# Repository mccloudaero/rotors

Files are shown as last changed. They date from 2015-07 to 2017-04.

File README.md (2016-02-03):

#Rotor Design and Build Repository
McCloud Aero Corporation

This repository contains the rotor designs and rotor analysis software created by McCloud Aero Corporation. The specific rotor designs contained in this repository were intended for use with the Goliath gas powered quadcopter, but the rotors could be used for other applications.  Goliath uses four rotors with two rotating clockwise (CW) and two counter-clockwise (CCW).  Any use of the data contained in this repository is without warranty.

##Repository Contents
 Documentation (this readme.txt file)
 Rotor Blade Element Analysis (RBEA) software (/rbea)
 Alpha Rotor Design and Build Files (/alpha)
  Counter-Clockwise Version (/CCW)
  Clockwise Version (/CW)
 Beta Rotor Design and Build Files  (/beta)
  Counter-Clockwise Version (/CCW)
  Clockwise Version (/CW)
 Crush Plate Designa and Build Files (/common)

###Alpha Rotor
The Alpha rotor was the original rotor design used for the Goliath quadcopter. This rotor has been tested approximatly 20 times and experienced thrust loads up to 50 lbs. This rotor has not seen long term testing. The pitch was found to be too large and required too much power at the proper RPM for Goliath. It could be applied to other vehicles.

###Beta Rotor
A redesign of the alpha rotor, with the pitch at the tip reduced.  Has not been tested.
 
###Design Files
Each rotor contains the following Design Files:<br>
 *.AD_PRT		- CAD file, Cubify Design Native CAD format (The software used to design the rotors)<br>
 *.stp			- CAD file, STEP format<br>
 *.igs			- CAD file, IGES format<br>
 *_final.stl		- STL file of the final rotor shape<br>
 *_mill_shape.stl	- STL file of the shape to be milled<br>
 *.png			- Image of the rotor design<br>
 
##Design Process
The CAD was built using Cubify Design. The STL file was generated using the folowing settings:<br>
 Units: Inches<br>
 Format: ASCII<br>
 Normal Deviation: 2.0 deg<br>
 Surface Deviation: 0.02<br>
 Maximum Cell Size: 0.5<br>

To create the mill shape in the CAD file:<br>
 1. Unsuppress the Machine Supports
 2. Unsuppress the Hub Support
 3. Unsuppress the Hub Support Mirror
 4. Suppress the Mounting Holes
 5. Suppress the Center Hole
 6. Suppress the Trim Tip

##Toolpath Generation
The toolpaths contained in this repository were generated using MeshCam (http://www.grzsoftware.com/). The rough steps used to create the toolpaths are below.  Feed Rates and plunge rates were driven by the need to go slower though the birch stiffness present in the propeller blanks.

 1. Load mill shape
 2. Choose 2-Sided Maching
 3. Define Stock Size 38" x 10" x 1.75"
 4. Create Top & Bottom Rough Tool Paths with 0.25" diameter tool
  1. Depth per Pass 0.25"
  2. Stepover 0.125"
  3. Feed Rate 60 in/min 
  4. Plunge Rate 10 in/min
  5. Stock to leave 0.05"
 5. Create Top and Bottom Finish X Only Tool Paths with 0.25" diameter tool
  1. Stepover 0.0.0833"
  2. Feed Rate 60 in/min 
  3. Plunge Rate 10 in/min
 6. Create Top and Bottom Finish X Only Tool Paths with 0.25" diameter tool
  1. Stepover 0.0.0833"
  2. Feed Rate 60 in/min 
  3. Plunge Rate 10 in/min

##Build Process
For each rotor there are two STL files, one is the milled shape and the second is the final rotor shape. Each rotor is machined out of a 38" x 10" x 1.75" foam block.  The machining region is 36" x 8" x 1.75", leaving an inch extra on each of the side and no extra on the top and bottom. To machine the part double sided accurately, alignment pins are helpful.  To use the pins, the same alignment holes drilled into rotor need to be drilled into the spoil board (if possible).  Dowel rods (1/4" diameter) are used as alignment pins.

Tool bits needed are:
1/4" End Mill  (>=1.75" Long) for the Finishing Passes

###Machining Steps
 1. Machine the Top
  1. Roughing pass: Start with the 1/2" End Mill and run rotor_XXX_top_rough
  2. Finishing pass (X direction): Switch to 1/4" End Mill and run rotor_XXX_top_finish_x_only
  3. Finishing pass (Y direction): Run rotor_XXX_top_finish_y_only
  4. Drill the Alignment Holes: Run rotor_XXX_top_drill_holes
 2. Flip the block over and re-mount using the alignment holes and pins
 3. Machine the Bottom
  1. Roughing pass: Run rotor_XXX_bottom_rough (Note: roughing stays with 1/4" bit because of the fragile part)
  2. Finishing pass (X direction): Run rotor_XXX_bottom_finish_x_only
  3. Finishing pass (Y direction): Run rotor_XXX_bottom_finish_y_only

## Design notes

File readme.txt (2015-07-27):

Rotor Design and Build Repository
McCloud Aero Corporation

This repository contains the rotor designs and rotor analysis software created by McCloud Aero Corporation. The specific rotor designs contained in this repository were intended for use with the Goliath gas powered quadcopter, but the rotors could be used for other applications.  Goliath uses four rotors with two rotating clockwise (CW) and two counter-clockwise (CCW).  Any use of the data contained in this repository is without warranty.

==Repository Contents==
 Documentation (this readme.txt file)
 Rotor Blade Element Analysis (RBEA) software (/rbea)
 Alpha Rotor Design and Build Files (/alpha)
  Counter-Clockwise Version (/CCW)
  Clockwise Version (/CW)
 Beta Rotor Design and Build Files  (/beta)
  Counter-Clockwise Version (/CCW)
  Clockwise Version (/CW)
 Crush Plate Designa and Build Files (/common)

== Alpha Rotor ==
The Alpha rotor was the original rotor design used for the Goliath quadcopter. This rotor has been tested approximatly 20 times and experienced thrust loads up to 50 lbs. This rotor has not seen long term testing. The pitch was found to be too large and required too much power at the proper RPM for Goliath. It could be applied to other vehicles.

== Beta Rotor ==
A redesign of the alpha rotor, with the pitch at the tip reduced.  Has not been tested.
 
==Design Files==
Each rotor contains the following Design Files:
 *.AD_PRT		- CAD file, Cubify Design Native CAD format (The software used to design the rotors)
 *.stp			- CAD file, STEP format
 *.igs			- CAD file, IGES format
 *_final.stl		- STL file of the final rotor shape
 *_mill_shape.stl	- STL file of the shape to be milled
 *.png			- Image of the rotor design
 
==Design Process==
The CAD was built using Cubify Design. The STL file was generated using the folowing settings:
 Units: Inches
 Format: ASCII
 Normal Deviation: 2.0 deg
 Surface Deviation: 0.02
 Maximum Cell Size: 0.5

To create the mill shape in the CAD file:
1) Unsuppress the Machine Supports 
2) Unsuppress the Hub Support
3) Unsuppress the Hub Support Mirror
4) Suppress the Mounting Holes
5) Suppress the Center Hole
6) Suppress the Trim Tip

==Toolpath Generation==
The toolpaths contained in this repository were generated using MeshCam (http://www.grzsoftware.com/). The rough steps used to create the toolpaths are below.  Feed Rates and plunge rates were driven by the need to go slower though the birch stiffness present in the propeller blanks.

1) Load mill shape
2) Choose 2-Sided Maching
3) Define Stock Size 38" x 10" x 1.75"
4) Create Top & Bottom Rough Tool Paths with 0.25" diameter tool
 A) Depth per Pass 0.25"
 B) Stepover 0.125"
 C) Feed Rate 60 in/min 
 D) Plunge Rate 10 in/min
 E) Stock to leave 0.05"
5) Create Top and Bottom Finish X Only Tool Paths with 0.25" diameter tool
 A) Stepover 0.0.0833"
 B) Feed Rate 60 in/min 
 C) Plunge Rate 10 in/min
6) Create Top and Bottom Finish X Only Tool Paths with 0.25" diameter tool
 A) Stepover 0.0.0833"
 B) Feed Rate 60 in/min 
 C) Plunge Rate 10 in/min

==Build Process==
For each rotor there are two STL files, one is the milled shape and the second is the final rotor shape. Each rotor is machined out of a 38" x 10" x 1.75" foam block.  The machining region is 36" x 8" x 1.75", leaving an inch extra on each of the side and no extra on the top and bottom. To machine the part double sided accurately, alignment pins are helpful.  To use the pins, the same alignment holes drilled into rotor need to be drilled into the spoil board (if possible).  Dowel rods (1/4" diameter) are used as alignment pins.

Tool bits needed are:
1/4" End Mill  (>=1.75" Long) for the Finishing Passes

==Machining Steps==
1) Machine the Top
 A) Roughing pass: Start with the 1/2" End Mill and run rotor_XXX_top_rough
 B) Finishing pass (X direction): Switch to 1/4" End Mill and run rotor_XXX_top_finish_x_only
 C) Finishing pass (Y direction): Run rotor_XXX_top_finish_y_only
 D) Drill the Alignment Holes: Run rotor_XXX_top_drill_holes
2) Flip the block over and re-mount using the alignment holes and pins
3) Machine the Bottom
 A) Roughing pass: Run rotor_XXX_bottom_rough (Note: roughing stays with 1/4" bit because of the fragile part)
 B) Finishing pass (X direction): Run rotor_XXX_bottom_finish_x_only
 C) Finishing pass (Y direction): Run rotor_XXX_bottom_finish_y_only

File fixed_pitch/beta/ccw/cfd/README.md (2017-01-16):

#CFD Analysis

#. Create simplified geometry (CAD)
##. Export as STEP 214
#. Mesh simplified geometry (gmsh)

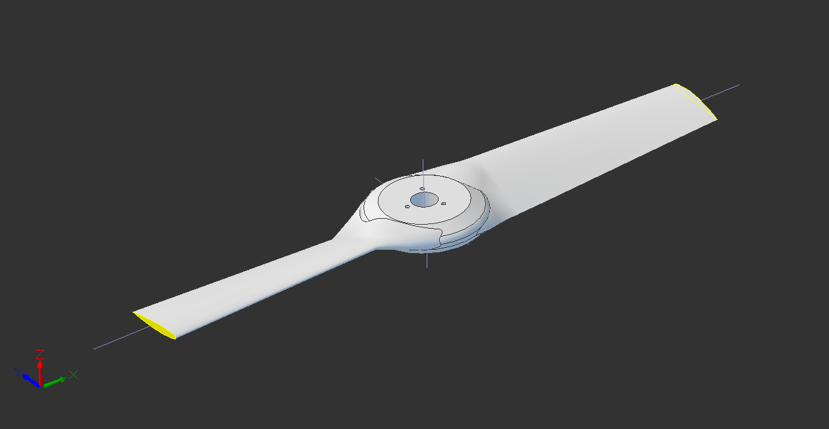
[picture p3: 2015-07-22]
fixed_pitch/beta/CCW/rotor_ccw.png

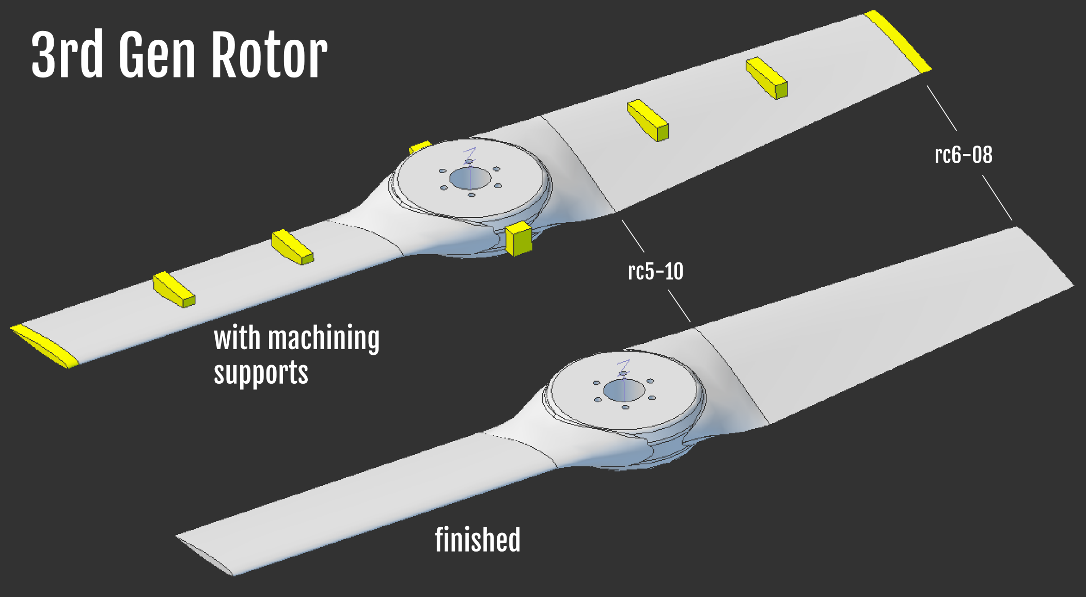
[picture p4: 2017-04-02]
fixed_pitch/gamma/ccw/rotor_before_and_after.png

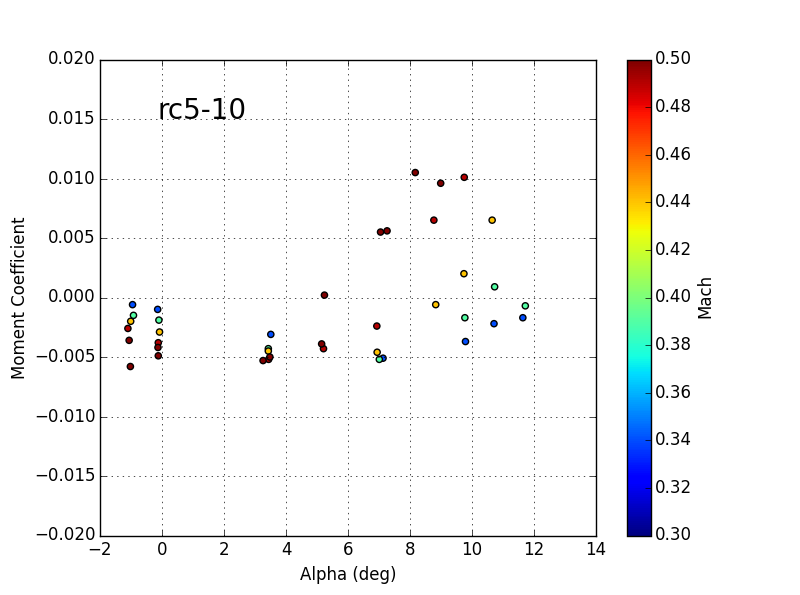
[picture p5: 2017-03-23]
rbea/airfoils/rc5_10_moment.png

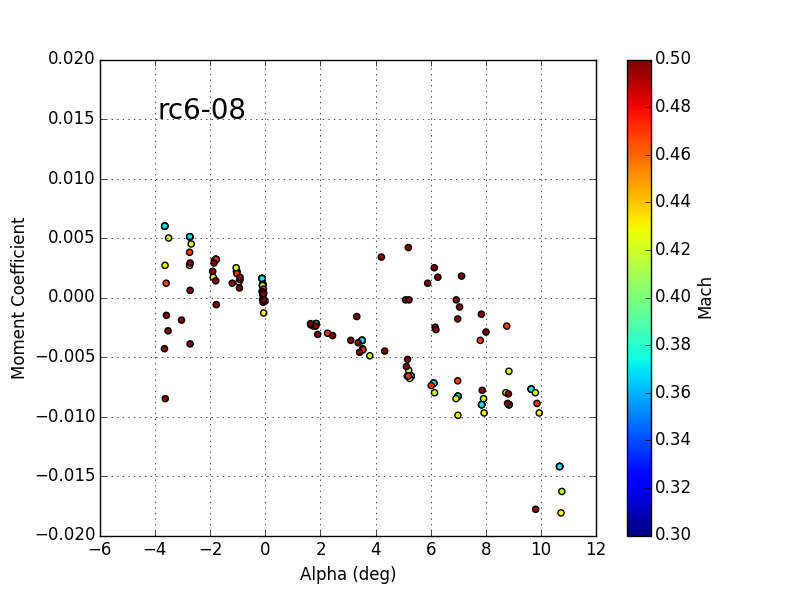
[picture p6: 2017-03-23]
rbea/airfoils/rc6-08_moment.png

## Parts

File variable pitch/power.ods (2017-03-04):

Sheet: Power Budget
Power Budget
Item | mA | Voltage | Count | Watts | Source
Servos | 900 | 6.00 | 2 | 10.8 | https://www.quora.com/Which-battery-should-I-use-to-power-5-servo-MG996R-motors
ESP32 | 260 | 3.30 | 1 | 0.858 | https://cdn.sparkfun.com/datasheets/IoT/esp32_datasheet_en.pdf
 |  |  | Total | 11.658

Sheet: Coil Sizing
Coil Sizing
Min Power | 12 | Watts
Min Voltage | 5 | Volts
Current | 2.4 | Amps
# of Coils | 6
Current per Coil | 0.4 | -> | 25 Gauge min
Turns per Coil | 100
RPM | t | Vmax
3000 | 0.0033333333 | 8.10
3740 | 0.0026737968 | 10.10
3940 | 0.0025380711 | 10.64

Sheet: Magnet Wire Data
Gauge | Resistance (Ohms/1000 ft) | Resistance (Ohms/km) | Max Current Amps)
0000 (4/0) | 0.049 | 0.16072 | 302
000 (3/0) | 0.0618 | 0.202704 | 239
00 (2/0) | 0.0779 | 0.255512 | 190
0 (1/0) | 0.0983 | 0.322424 | 150
1 | 0.1239 | 0.406392 | 119
2 | 0.1563 | 0.512664 | 94
3 | 0.197 | 0.64616 | 75
4 | 0.2485 | 0.81508 | 60
5 | 0.3133 | 1.027624 | 47
6 | 0.3951 | 1.295928 | 37
7 | 0.4982 | 1.634096 | 30
8 | 0.6282 | 2.060496 | 24
9 | 0.7921 | 2.598088 | 19
10 | 0.9989 | 3.276392 | 15
11 | 1.26 | 4.1328 | 12
12 | 1.588 | 5.20864 | 9.3
13 | 2.003 | 6.56984 | 7.4
14 | 2.525 | 8.282 | 5.9
15 | 3.184 | 10.44352 | 4.7
16 | 4.016 | 13.17248 | 3.7
17 | 5.064 | 16.60992 | 2.9
18 | 6.385 | 20.9428 | 2.3
19 | 8.051 | 26.40728 | 1.8
20 | 10.15 | 33.292 | 1.5
21 | 12.8 | 41.984 | 1.2
22 | 16.14 | 52.9392 | 0.92
23 | 20.36 | 66.7808 | 0.729
24 | 25.67 | 84.1976 | 0.577
25 | 32.37 | 106.1736 | 0.457
26 | 40.81 | 133.8568 | 0.361
27 | 51.47 | 168.8216 | 0.288
28 | 64.9 | 212.872 | 0.226
29 | 81.83 | 268.4024 | 0.182
30 | 103.2 | 338.496 | 0.142
31 | 130.1 | 426.728 | 0.113
32 | 164.1 | 538248 | 0.091
33 | 206.9 | 678.632 | 0.072
34 | 260.9 | 855.752 | 0.056
35 | 329 | 1079.12 | 0.044
36 | 414.8 | 1360 | 0.035
37 | 523.1 | 1715 | 0.0289
38 | 659.6 | 2163 | 0.0228
39 | 831.8 | 2728 | 0.0175
40 | 1049 | 3440 | 0.0137

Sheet: Baseline Design
RPM | Voltage | Current | Watts | t | AB
512 | 2 | 1 | 2 | 1.95E-02 | 0.0001302083
818 | 4.78 | 1.47 | 7 | 1.22E-02 | 0.000194784
1022 | 6.8 | 1.7 | 11.7 | 9.78E-03 | 0.0002217873
1288 | 9.5 | 2 | 19 | 7.76E-03 | 0.0002458592
1611 | 12.8 | 2.3 | 29.4 | 6.21E-03 | 0.0002648459
1992 | 16.6 | 2.7 | 45 | 5.02E-03 | 0.0002777778
# of Coils | 6
Current per Coil | 0.35
Turns per Coil | 300

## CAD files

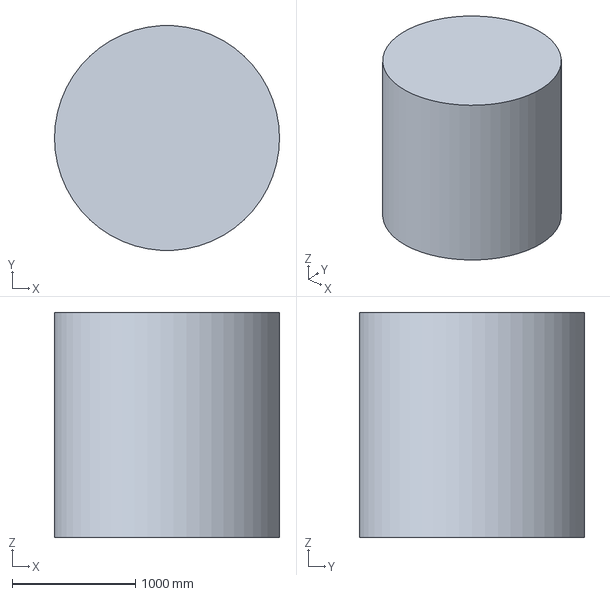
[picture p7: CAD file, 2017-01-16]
fixed_pitch/beta/ccw/cfd/rotor_ccw_cfd_domain.stp
1828.8 x 1825.7 x 1828.8 mm

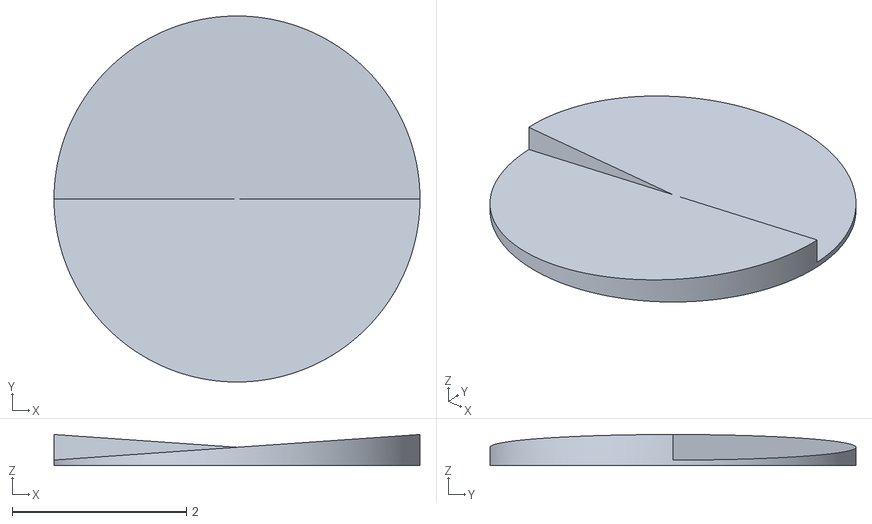
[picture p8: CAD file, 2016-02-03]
adjustment plate/adjustment_plate_cw_no_holes.stl
4.20 x 4.20 x 0.356

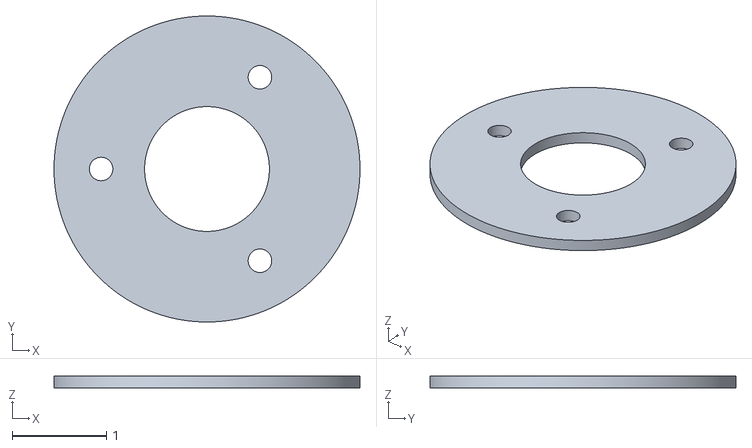
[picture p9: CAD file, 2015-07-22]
common/crush_plate/crush_plate.stl
3.25 x 3.25 x 0.125

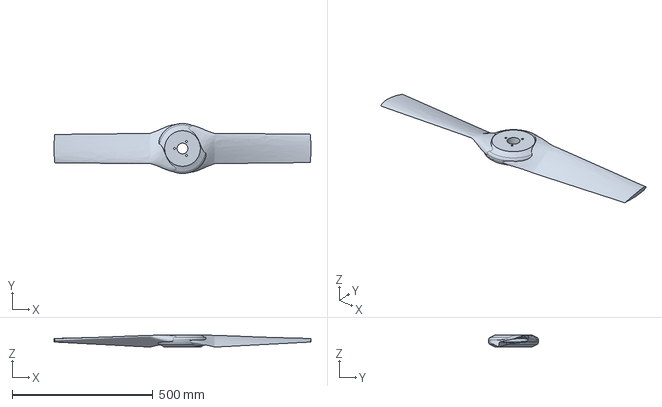
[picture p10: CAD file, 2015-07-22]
fixed_pitch/beta/CCW/rotor_ccw.stp
914.4 x 177.7 x 44.5 mm

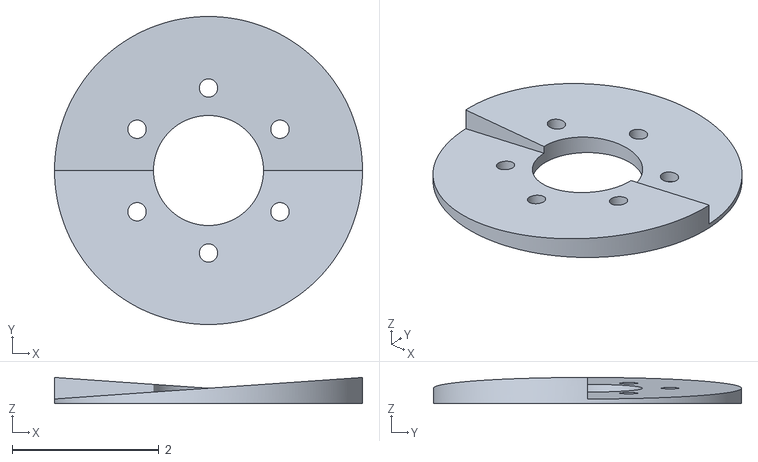
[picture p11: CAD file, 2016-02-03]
adjustment plate/adjustment_plate_cw_with_holes.stl
4.20 x 4.20 x 0.356

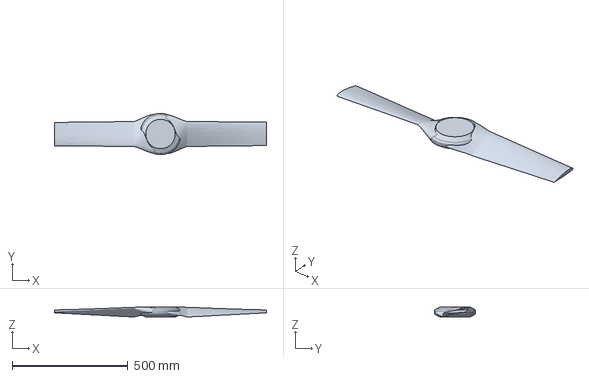
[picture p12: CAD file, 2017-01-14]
fixed_pitch/beta/ccw/cfd/rotor_ccw_cfd_clean.stp
914.4 x 177.7 x 44.5 mm

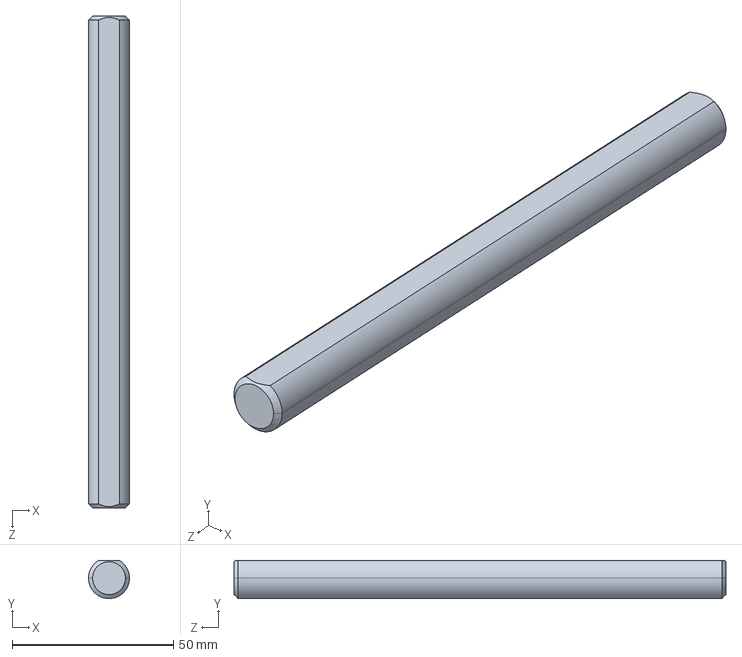
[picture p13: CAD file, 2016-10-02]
variable pitch/design_A/8632T146_D-PROFILE SHAFT.STEP
12.7 x 11.8 x 152.4 mm

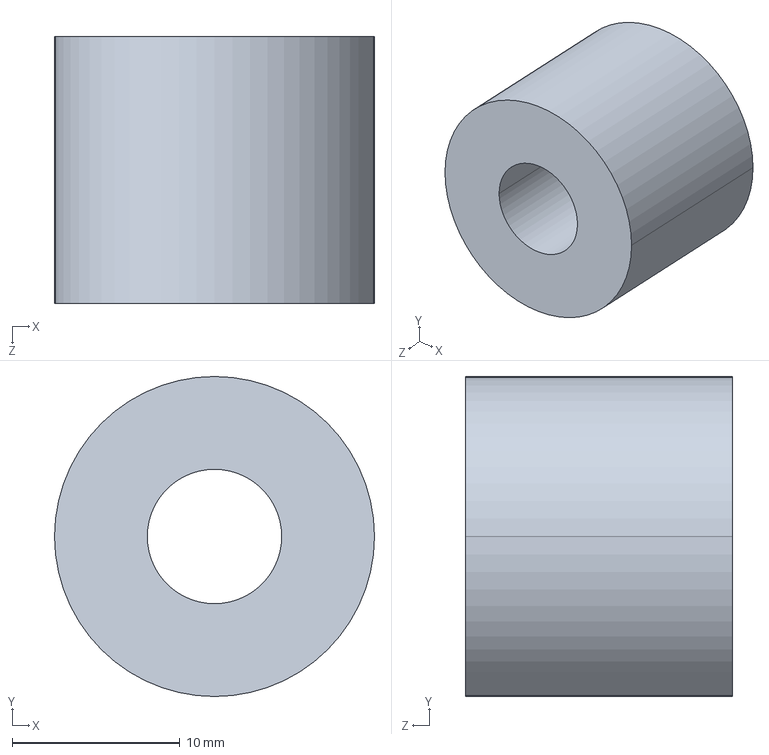
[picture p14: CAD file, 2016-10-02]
variable pitch/design_B/92320A728_SS UNTHRD SPACER.STEP
19.1 x 19.1 x 15.9 mm

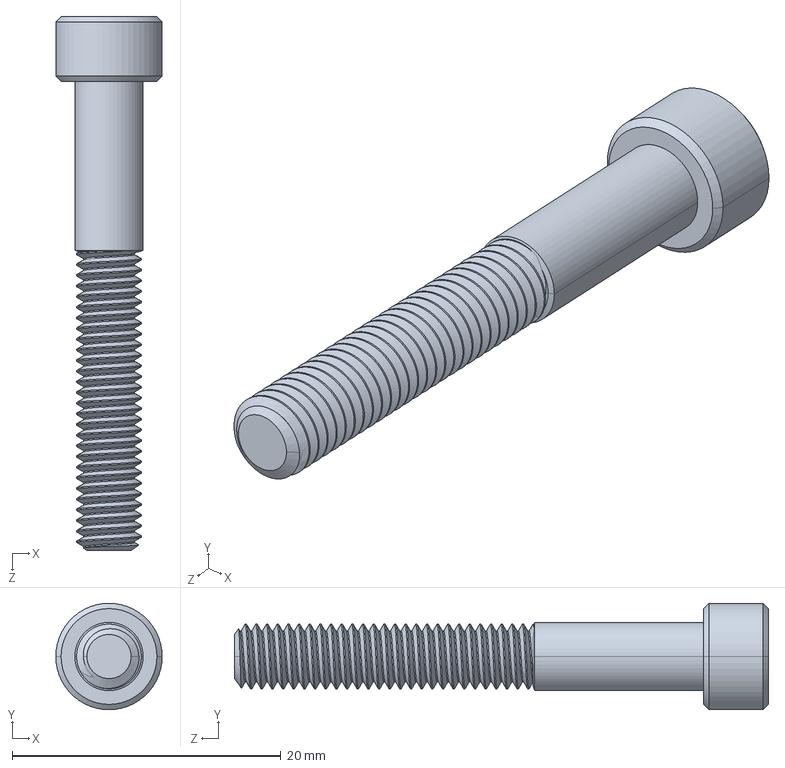
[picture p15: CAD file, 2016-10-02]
variable pitch/design_A/90128A132_ZNC-PLTD ALLOY STL SCKT HEAD CAP SCREW.STEP
7.92 x 7.92 x 39.8 mm

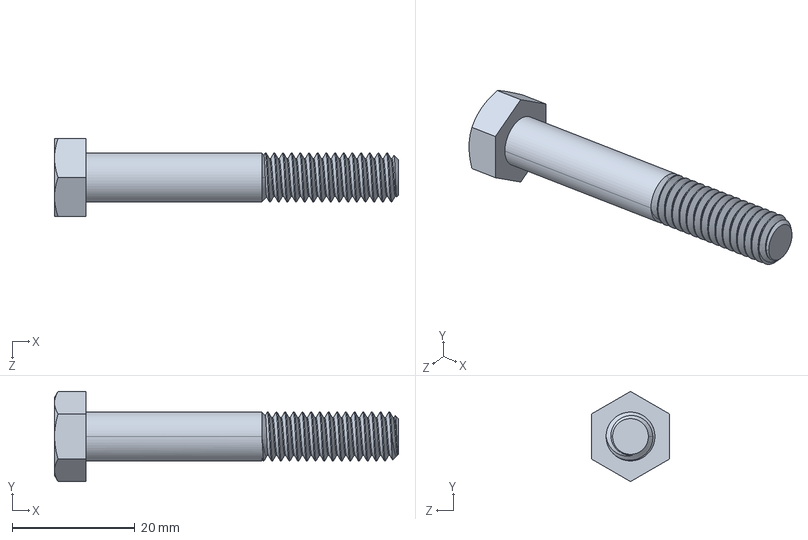
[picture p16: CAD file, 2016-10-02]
variable pitch/design_B/92245A591_MIL. SPEC. SS HEX HEAD CAP SCREW.STEP
56.0 x 14.7 x 12.7 mm

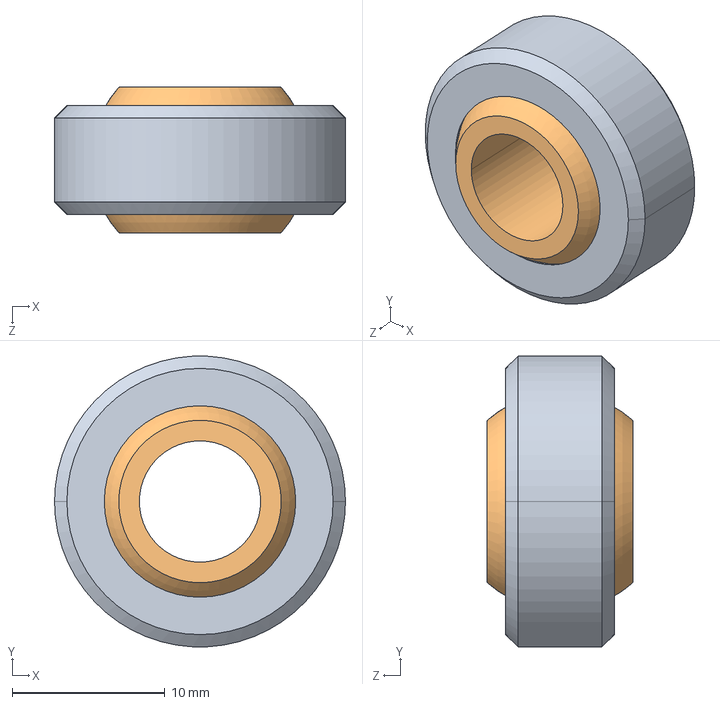
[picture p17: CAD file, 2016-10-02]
variable pitch/design_B/63215K530_STAINLESS STEEL BALL JOINT SWIVEL BEARING.STEP
19.1 x 19.0 x 9.52 mm

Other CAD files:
fixed_pitch/beta/ccw/cfd/cfd_domain_only.stp
fixed_pitch/beta/CCW/rotor_ccw.igs

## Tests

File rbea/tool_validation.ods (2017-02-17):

RPM | 3080
 | Thrust (N) | Power (kW)
Python BEM | 180.89 | 3.13
CFD | 183.21 | 2.8320207775
Difference | -1.28% | 9.52%
RPM | 3960
 | Thrust (N) | Power (kW)
Python BEM | 302.9 | 6.79
CFD | 309 | 6.0299095174
Difference | -2.01% | 11.19%

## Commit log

2015-07-23 Renamed Files for beta rotor
    [rotor_20150712B.igs, rotor_20150712B.stp, rotor_ccw.igs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]
2015-07-23 Updated Mill Shape
2015-07-25 Added rotor blade element analysis code
2015-07-27 Changed top roughing toolpath for beta rotor to use 1/4" tool bit
2016-02-03 added adjustment plate
    [adjustment_plate_cw_no_holes.stl, adjustment_plate_cw_with_holes.stl]
2016-10-02 added variable pitch dir, moved prior designs to fixed pitch dir
    [63215K530_STAINLESS STEEL BALL JOINT SWIVEL BEARING.STEP, 8632T146_D-PROFILE SHAFT.STEP, 90128A132_ZNC-PLTD ALLOY STL SCKT HEAD CAP SCREW.STEP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]
2016-10-10 initial work on 3rd gen rotor
    [rotor_data.ods]
2017-01-14 various updates
    [NACA_0012_half.csv, NACA_0012_half.ods, naca_shapes.ods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]
2017-01-16 created domain files for beta/ccw cfd
    [cfd_domain_only.stp, rotor_ccw_cfd_clean.stp, rotor_ccw_cfd_domain.stp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]
2017-02-03 upgrades to rotor.py to use splines for airfoil data
2017-02-16 old results for beta rotor
2017-02-16 added initial gamma rotor candidate
2017-02-16 added tool validation data
    [tool_validation.ods]
2017-02-17 added Power prediction comparisons
    [tool_validation.ods]
2017-02-17 initial files for gamma cad
    [rc6-08.ods]
2017-02-27 addition of rc4 and rc5 airfoil data
    [rc4-10.ods, rc5-10.ods]
2017-02-27 rotor.py updates for blending airfoils
2017-02-27 added outputs from previously updated rotor.py
2017-02-28 fixed error in rc5-10 coordinates
    [rc5-10.ods]
2017-03-02 updates to rotor.py to calculate blade moments
2017-03-03 added radius to gamma rotor hub
2017-03-04 added variable pitch power estimates
    [power.ods]
2017-03-23 updated rotor_ccw cad to color supports, exported images
2017-03-23 updates to variable pitch
    [prototype.fzz]
2017-04-02 added tool path for drilling hub after fiberglassing
